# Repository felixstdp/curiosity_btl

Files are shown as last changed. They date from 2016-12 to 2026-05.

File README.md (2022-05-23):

# curiosity_btl
files for Curiosity Bricolabs Technology Laboratory project

scale_1_10 folder for 1:10 scale model (this model has evolved to [Perseverance](https://github.com/felixstdp/Perseverance))
- 4 x 9g servos
- 6 x N20 dc motors

scale_1_5 folder for 1:5 scale model
- 4 x s3003/996 servos
- 6 x type 25D/2418 dc motors
- 2 x RC car steering turnbuckle
- 2S High capacity LiPo battery (e.g. https://www.batteryspace.com/li-ion-battery-14-8v-5-2ah-77wh-8a-rate-for-diving-light---un-38-3-passed.aspx)

.scad files for OpenScad
.stl files for printing
.ino files for Arduino
.jpg files for images

https://bricolabs.cc/wiki/en/proyectos/curiosity_btl (english)
https://bricolabs.cc/wiki/proyectos/curiosity_btl (spanish)

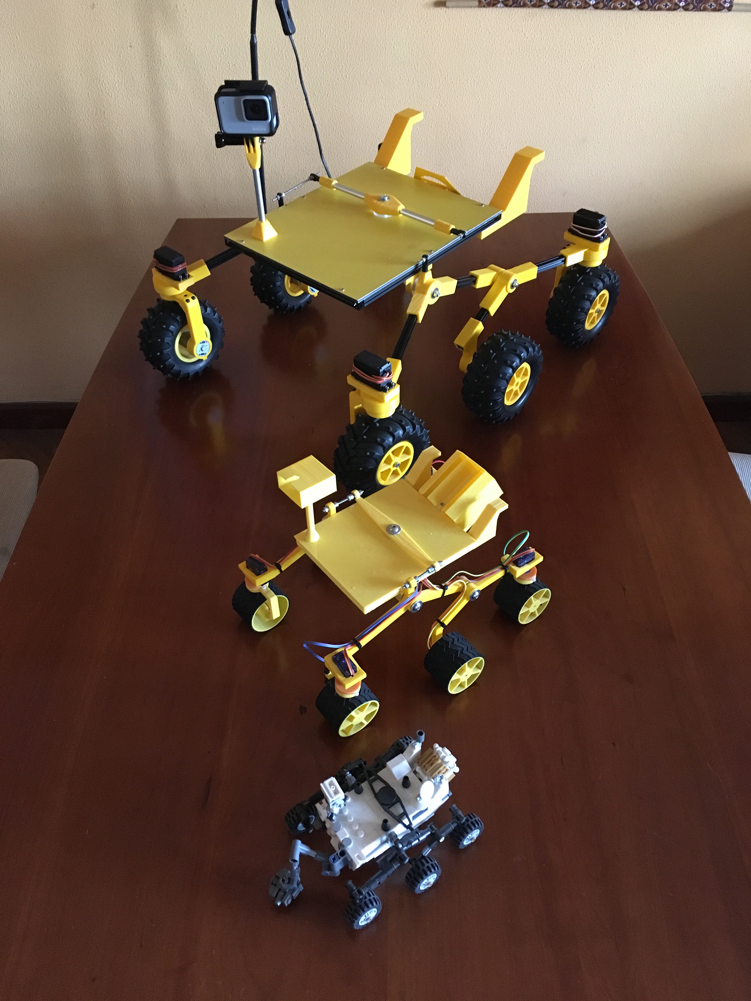
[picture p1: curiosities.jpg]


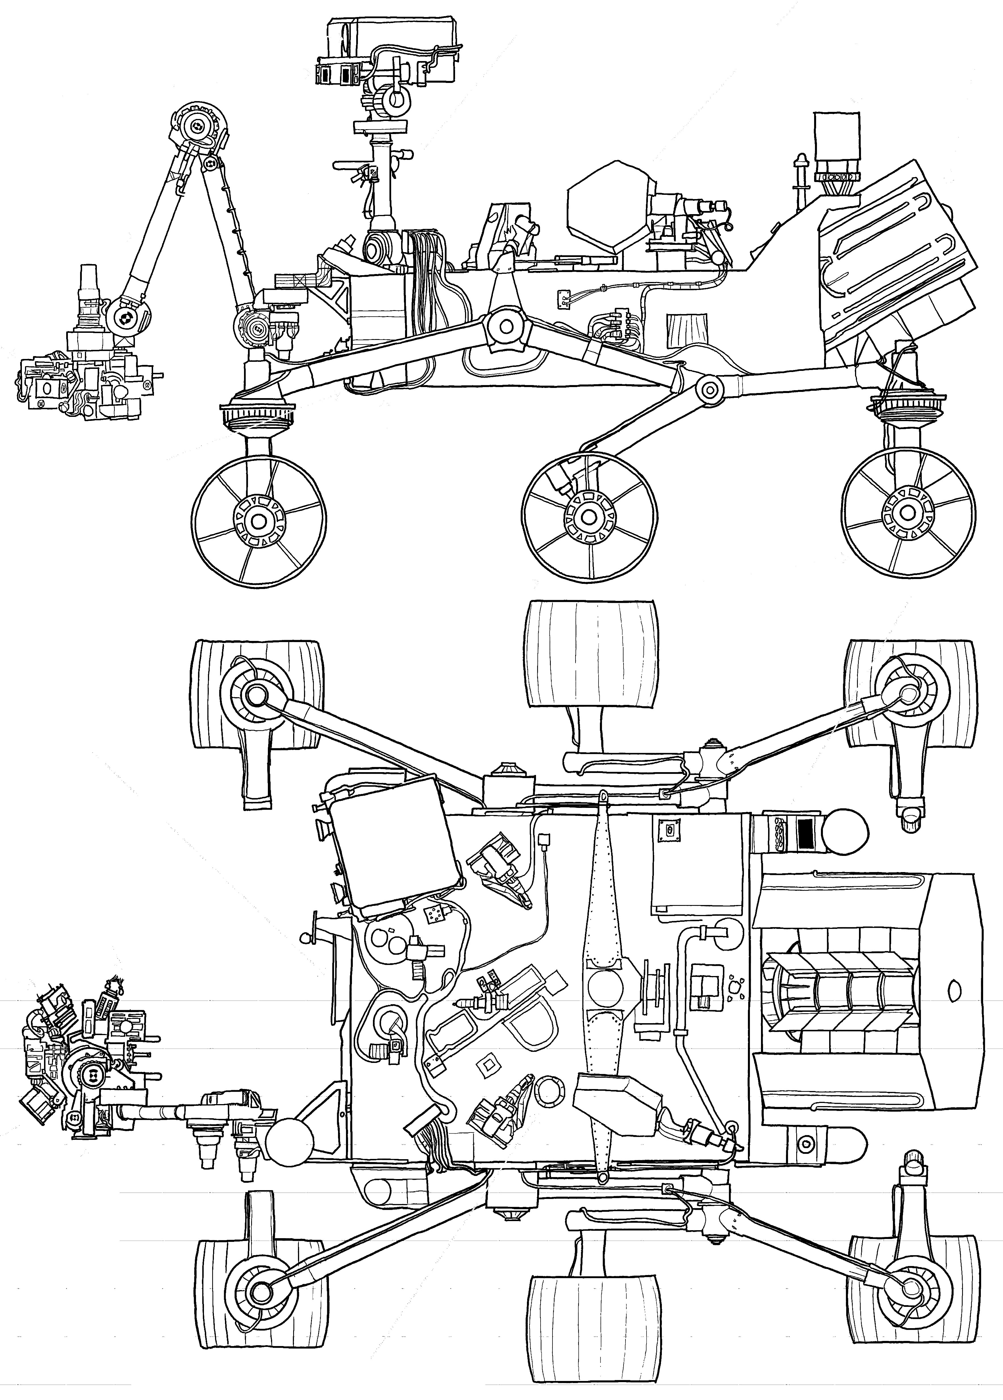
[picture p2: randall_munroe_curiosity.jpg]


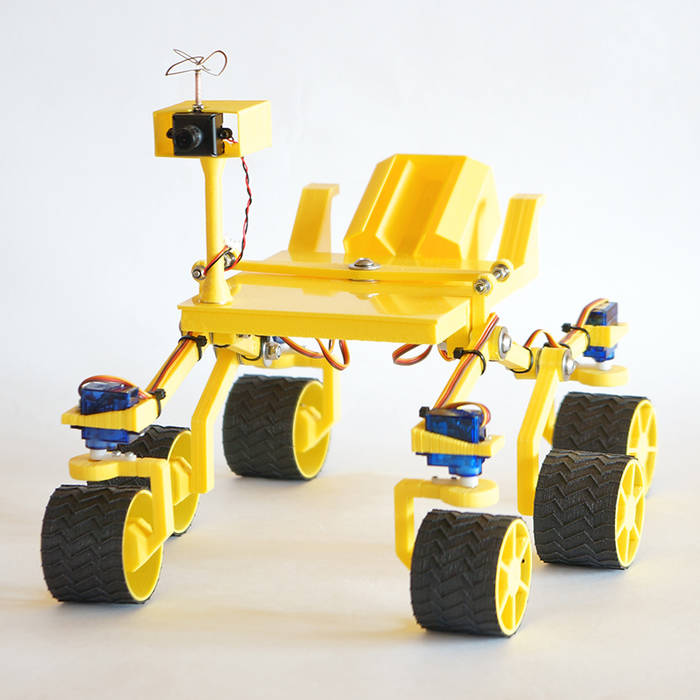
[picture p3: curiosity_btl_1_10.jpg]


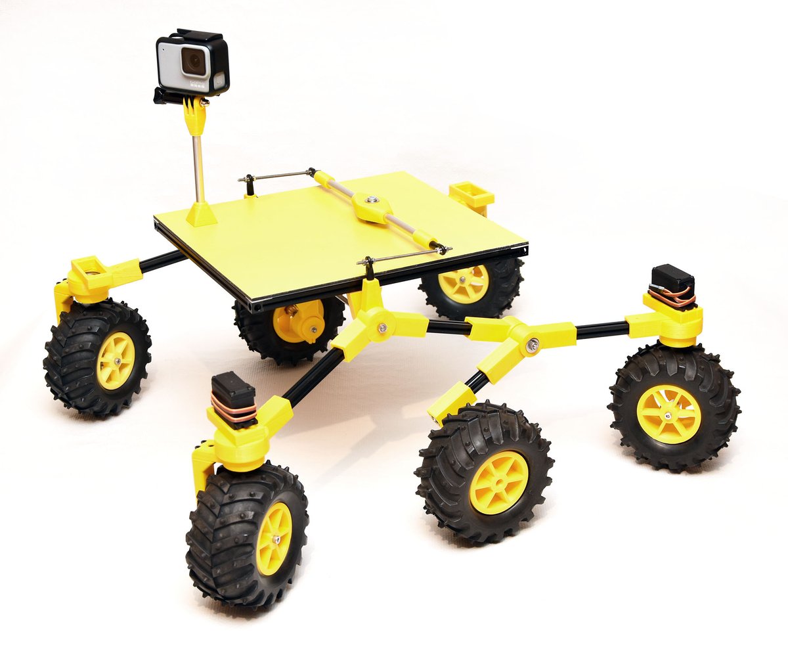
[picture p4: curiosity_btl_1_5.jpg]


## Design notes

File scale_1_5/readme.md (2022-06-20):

Versión con ruedas impresas

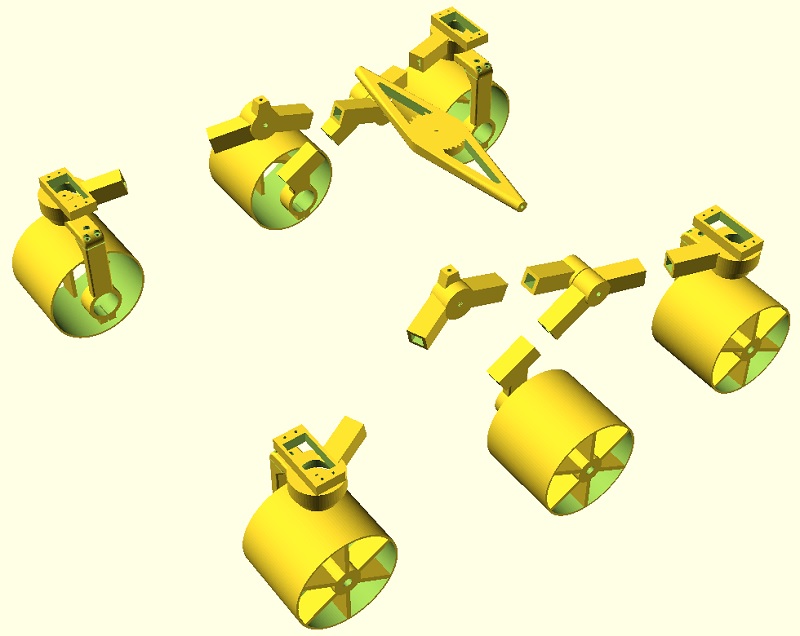
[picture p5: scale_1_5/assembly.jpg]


Versión con ruedas comerciales Pololu Dagu

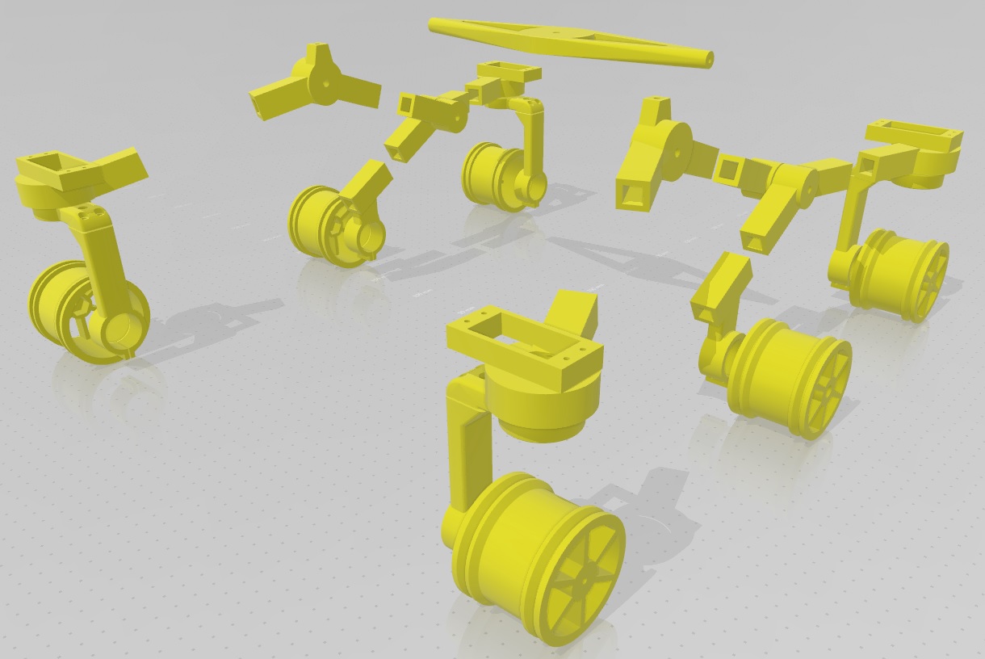
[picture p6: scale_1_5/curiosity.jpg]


BOM

- 4 servos s3003
- 6 motores 2418/25D
- 4 rodamientos 15x35x11
- 8 perfiles de aluminio 10x10mm (2 x 135mm, 2 x 125mm, 2 x 100mm, 2 x 115mm)
- 1 barra roscada M5
- 3 tornillos M5x45 + tuerca autoblocante + arandelas
- 30 tornillos M2.5 + tuerca
- 35 tornillos M3x10
- Plancha de Dibond de 3mm de grosor y 240x280mm. Opcional marco (sencillo/doble) de perfilería por debajo.

Las piezas con nombre 'atrezzo' no son funcionales, sólo decorativas para parecerse más al Curiosity MLS.

La impresión de todas las piezas necesita alrededor de 1kg de plástico y 60-70h. La impresión de las cubiertas (tyre) con material elástico 50-60h.

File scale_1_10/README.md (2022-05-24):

Lecacy code and project only for support.

If new, switch to [Perseverance](https://github.com/felixstdp/Perseverance)

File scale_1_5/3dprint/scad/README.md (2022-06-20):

There are two options for wheels:

- Commercial unit: Pololu Dagu
- 3D printed unit with flexible filament

rims (corner and center) and wheel_bracket_2 for the first options are labeled as 'dagu'.

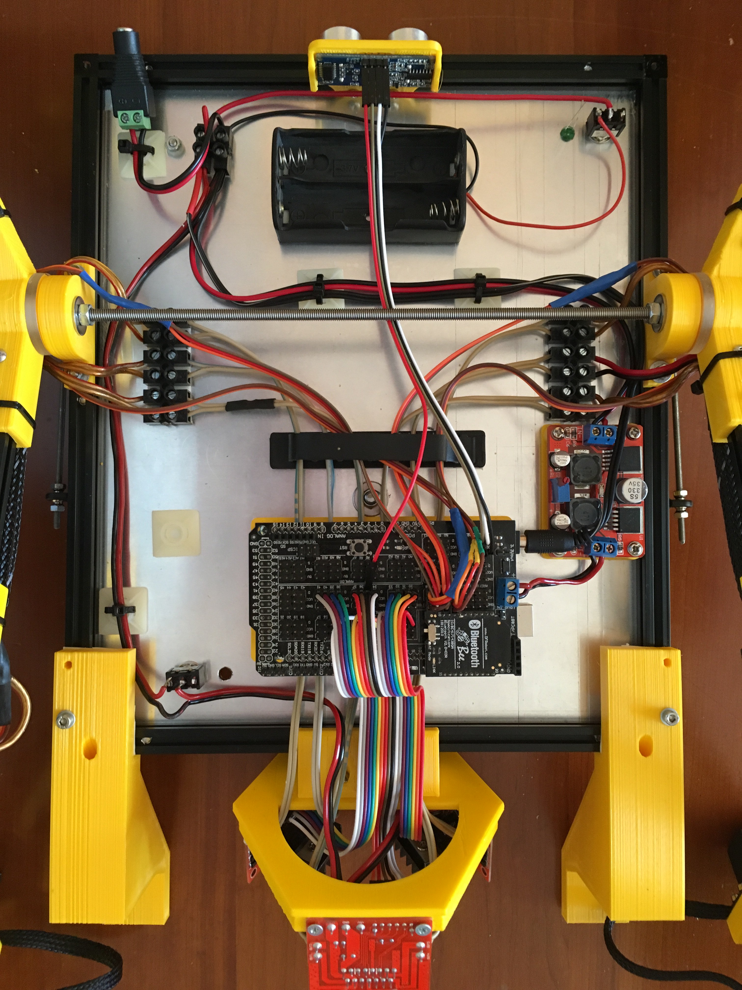
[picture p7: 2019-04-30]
cableado.jpg

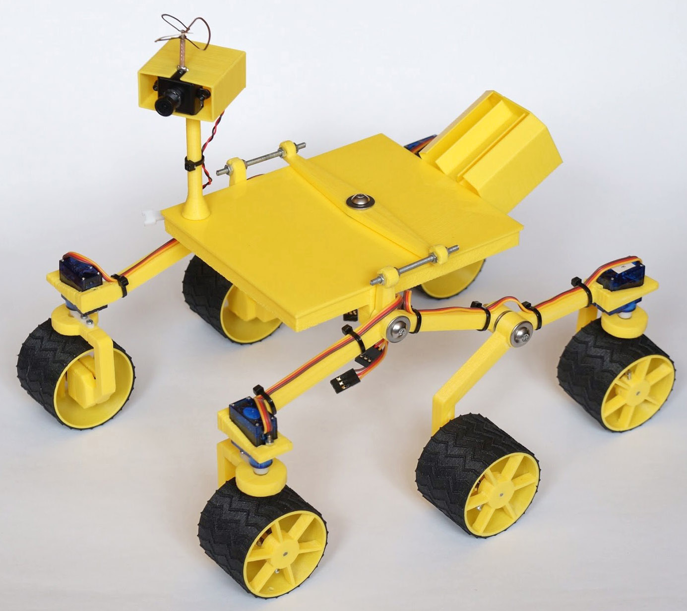
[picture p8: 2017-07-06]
scale_1_10/curiosity_btl.jpg

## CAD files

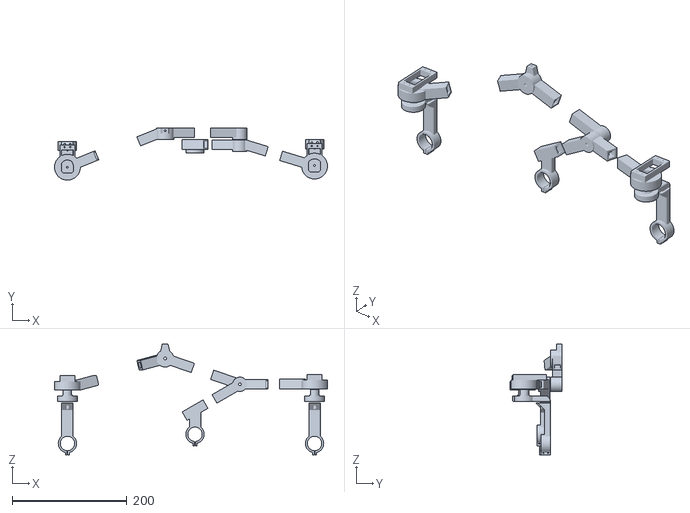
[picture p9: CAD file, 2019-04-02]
scale_1_5/assembly.stl
475.0 x 91.0 x 193.0

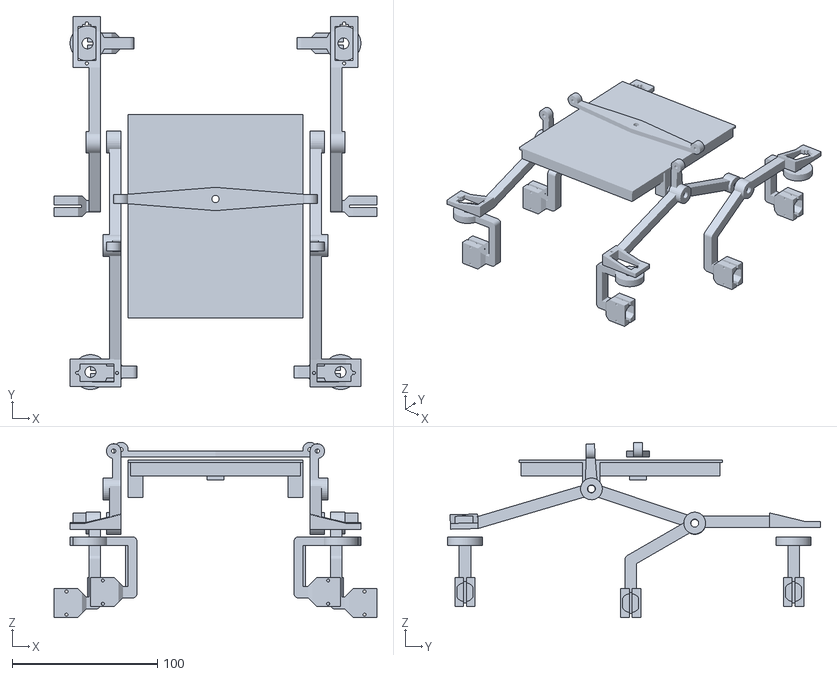
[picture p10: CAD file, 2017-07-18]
scale_1_10/stl/assembly.stl
222.0 x 256.5 x 120.5

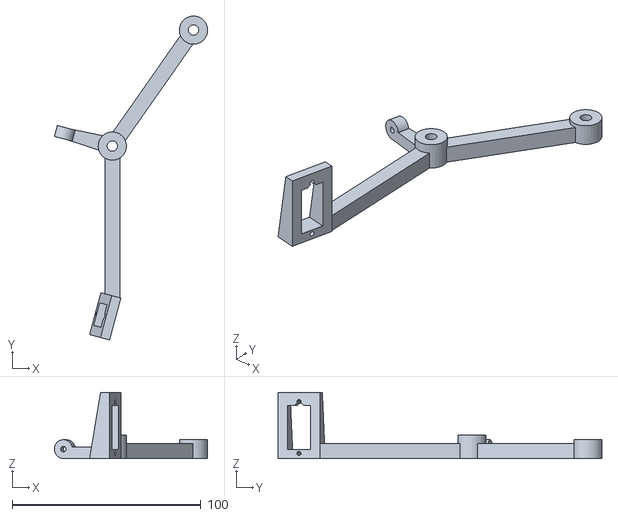
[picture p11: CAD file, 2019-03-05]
scale_1_10/stl/front_bogie.stl
81.2 x 171.7 x 35.0

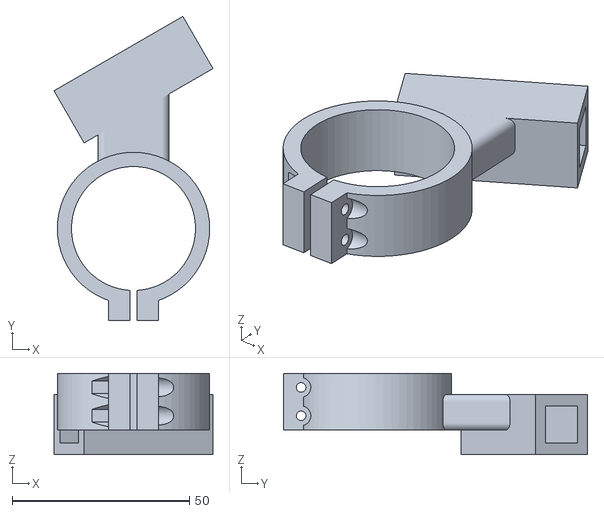
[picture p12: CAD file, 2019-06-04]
scale_1_5/3dprint/35mm_motors/rear_bogie_3_35mm.stl
44.9 x 85.9 x 23.0

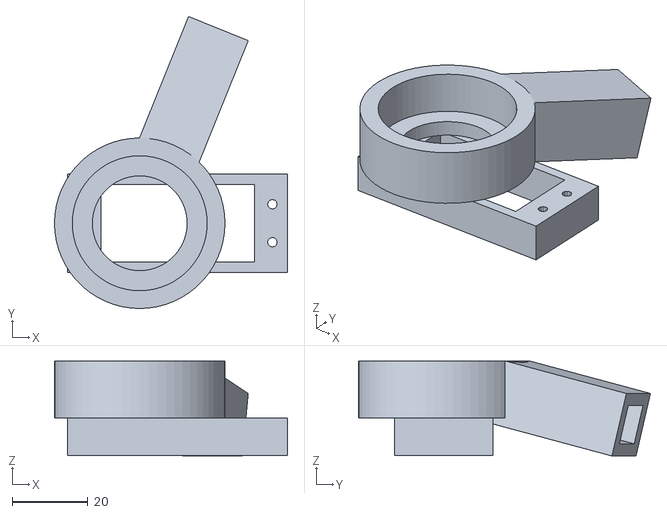
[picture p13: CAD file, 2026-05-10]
scale_1_5/3dprint/stl/front_bogie_1.stl
61.5 x 77.1 x 25.1

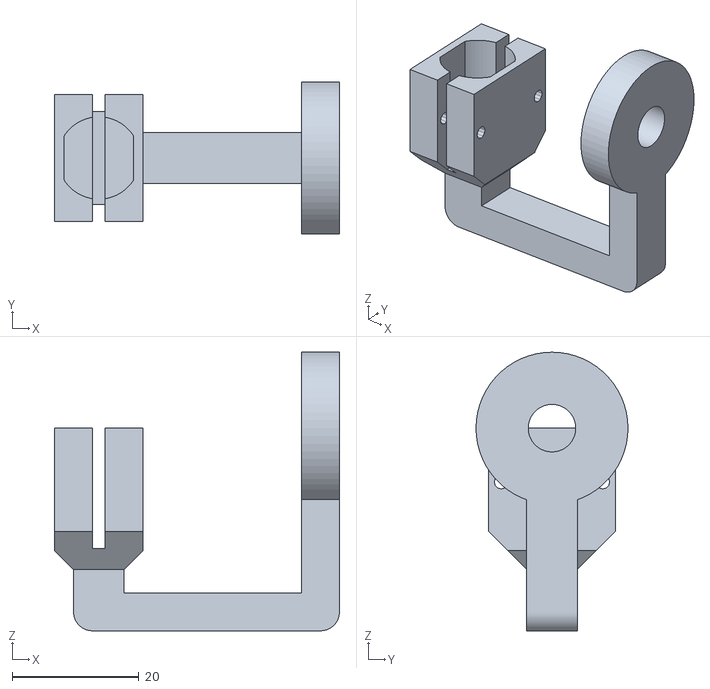
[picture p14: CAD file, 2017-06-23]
wheel_servo_braket.stl
45.0 x 24.0 x 44.0

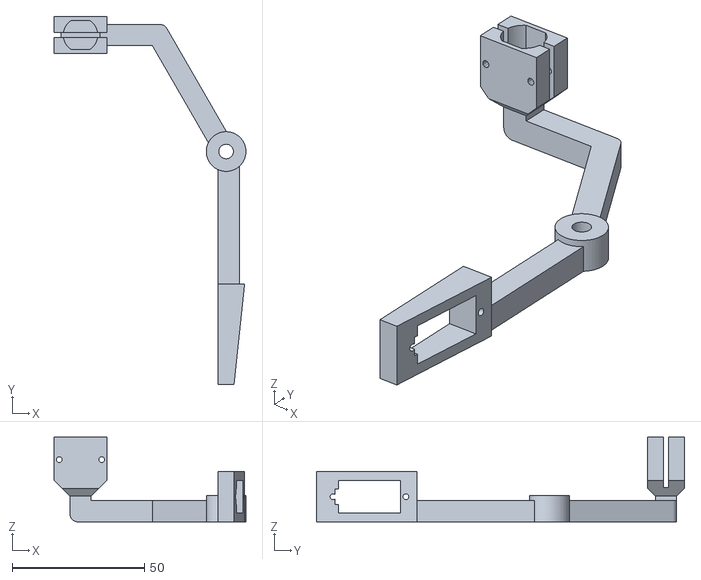
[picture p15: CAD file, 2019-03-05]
scale_1_10/stl/rear_bogie.stl
72.5 x 139.0 x 32.0

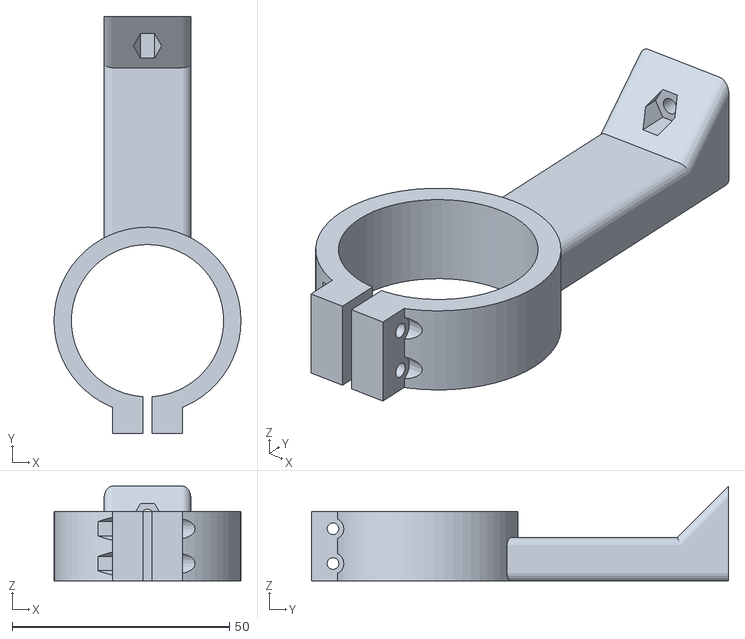
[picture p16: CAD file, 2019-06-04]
scale_1_5/3dprint/35mm_motors/wheel_bracket_1_35mm.stl
43.0 x 96.0 x 21.8

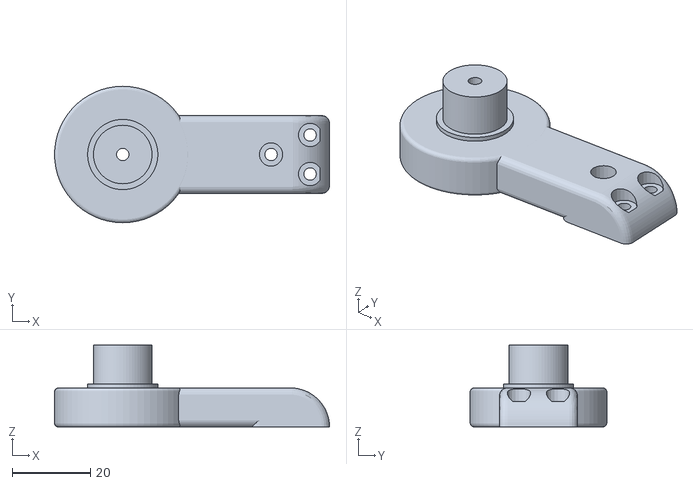
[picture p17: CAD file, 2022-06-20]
scale_1_5/3dprint/stl/wheel_bracket_2.stl
70.5 x 35.0 x 21.0

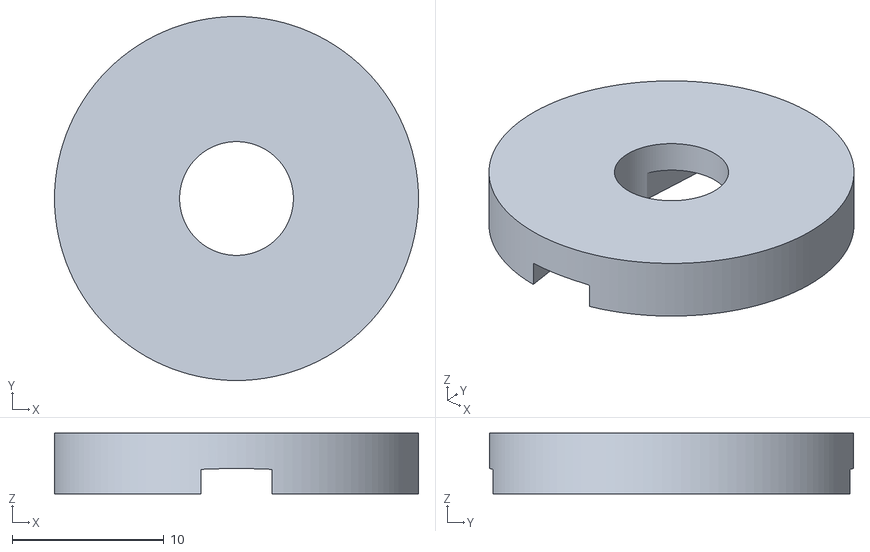
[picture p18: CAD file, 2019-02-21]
scale_1_10/stl/wheel_bracket_sandwich.stl
24.0 x 24.0 x 4.00

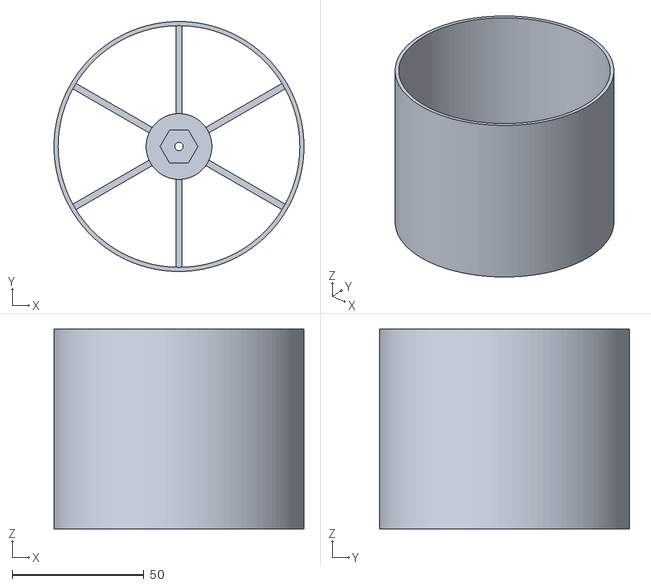
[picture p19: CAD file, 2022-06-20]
scale_1_5/3dprint/stl/corner_rim.stl
95.0 x 95.0 x 76.0

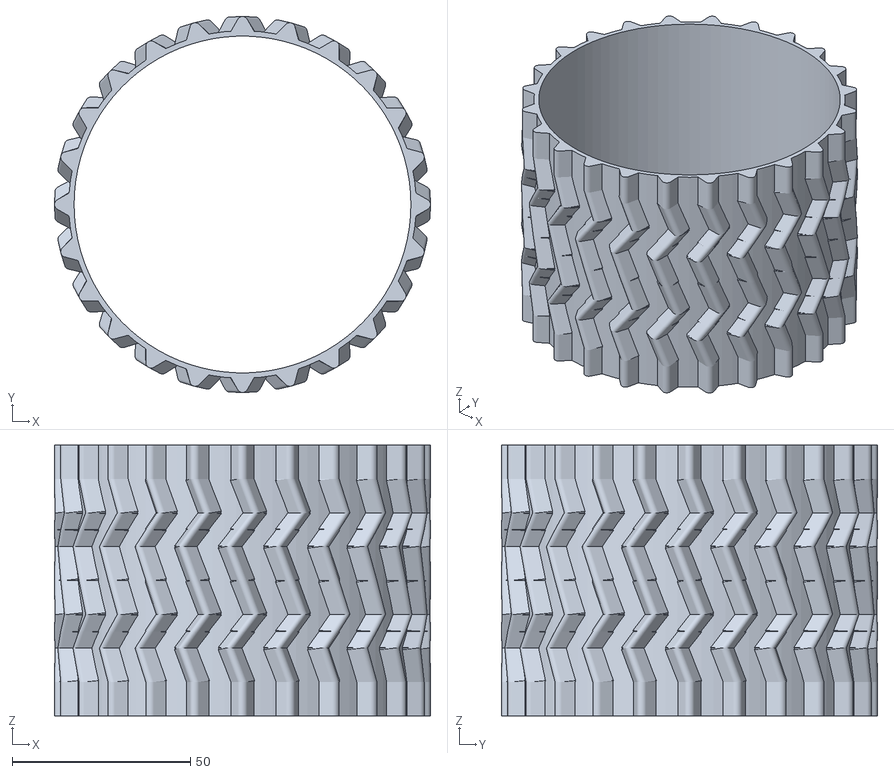
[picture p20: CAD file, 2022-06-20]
scale_1_5/3dprint/stl/tyre.stl
105.5 x 105.5 x 76.0

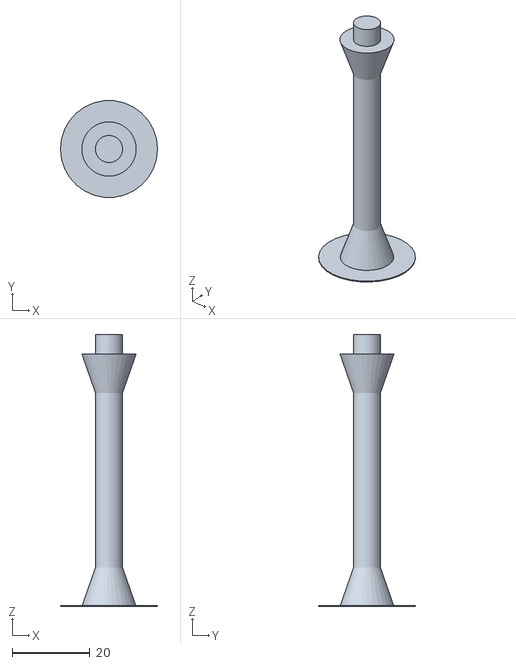
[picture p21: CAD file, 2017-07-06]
scale_1_10/stl/mastcam_post.stl
25.0 x 24.9 x 70.0

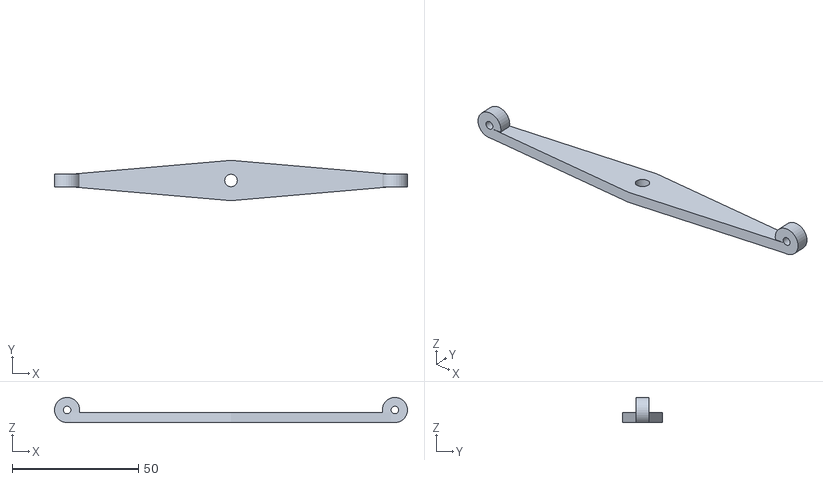
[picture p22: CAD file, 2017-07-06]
scale_1_10/stl/stabilizing_bar.stl
140.0 x 16.0 x 9.97

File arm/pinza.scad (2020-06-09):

$fn=240;
difference(){
union(){
difference(){
    cylinder(d=80,h=10);
    translate([0,0,-1])
    cylinder(d=77,h=12);
}
translate([7.5,0,0])
difference(){
    cylinder(d=65,h=10);
    translate([0,0,-1])
    cylinder(d=62,h=12);
}
translate([0,-.75,0])cube([40,1.5,10]);
rotate([0,0,45])translate([0,-.75,0])cube([40,1.5,10]);
rotate([0,0,67.5])translate([0,-.75,0])cube([40,1.5,10]);
rotate([0,0,90])translate([0,-.75,0])cube([40,1.5,10]);
rotate([0,0,112.5])translate([0,-.75,0])cube([40,1.5,10]);
rotate([0,0,-45])translate([0,-.75,0])cube([40,1.5,10]);
rotate([0,0,-67.5])translate([0,-.75,0])cube([40,1.5,10]);
rotate([0,0,-90])translate([0,-.75,0])cube([40,1.5,10]);
rotate([0,0,-112.5])translate([0,-.75,0])cube([40,1.5,10]);
}
    translate([45,0,-1])cylinder(d=45,h=12);
    translate([7.5,0,0])cylinder(d=62,h=12);
}

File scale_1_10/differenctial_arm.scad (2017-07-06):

$fn=30;

difference(){

linear_extrude(height=4)
polygon(
[[-63.5,2.5],
[0,8],
[63.5,2.5],
[63.5,-2.5],
[0,-8],
[-63.5,-2.5]]);

cylinder(d=5,h=10,center=true);
}

translate([65,0,5])rotate([90,0,0])
difference(){
cylinder(d=10,h=5,center=true);
cylinder(d=3,h=7,center=true);
}

translate([-65,0,5])rotate([90,0,0])
difference(){
cylinder(d=10,h=5,center=true);
cylinder(d=3,h=7,center=true);
}

translate([60,-2.5,0])
cube([5,5,1.5]);

translate([-65,-2.5,0])
cube([5,5,1.5]);

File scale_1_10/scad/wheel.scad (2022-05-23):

$fn=120;
difference(){
cylinder(d=47,h=38);
translate([0,0,-1])cylinder(d=45,h=40);
}
difference(){
union()
{
for(i=[0:60:300])
{
    rotate([0,0,i])translate([3,-0.75,0])
    cube(size=[20,1.5,10]);
} 
cylinder(d=16,h=10);
}
translate([0,0,-1])cylinder(d=3.35,h=21);
}
rotate([0,0,30])translate([1.15,-2,0])
cube(size=[2,4,10]);

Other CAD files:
scale_1_5/3dprint/stl/center_rim.stl
scale_1_5/3dprint/stl/rear_bogie_3.stl
scale_1_10/stl/mastcam_box.stl
scale_1_5/3dprint/stl/wheel_bracket_1.stl
scale_1_10/scad/wheel_bracket.scad
scale_1_10/mastcam_box.scad
scale_1_10/rtg.scad
scale_1_10/rtg_support.scad
scale_1_10/scad/assembly.scad
scale_1_10/scad/body_top.scad
scale_1_10/scad/front_bogie.scad
scale_1_10/scad/mastcam_box.scad
scale_1_10/scad/mastcam_post.scad
scale_1_10/scad/rear_bogie.scad
scale_1_10/scad/rear_support.scad
scale_1_10/scad/rtg.scad
scale_1_10/scad/rtg_support.scad
scale_1_10/scad/stabilizing_bar.scad
scale_1_10/scad/tyre.scad
scale_1_10/scad/wheel_bracket_r.scad
scale_1_10/scad/wheel_bracket_sandwich.scad
scale_1_10/stl/body_top.stl
scale_1_10/stl/rear_support.stl
scale_1_10/stl/rtg.stl
scale_1_10/stl/rtg_support.stl
scale_1_10/stl/tyre.stl
scale_1_10/stl/wheel.stl
scale_1_10/stl/wheel_bracket.stl
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

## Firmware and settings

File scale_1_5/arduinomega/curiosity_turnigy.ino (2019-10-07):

//       FRONT
//  M1S1       M6S6
//    \         /
//     \       /
//  M2-----------M5
//     /       \
//    /         \
//  M3S3       M4S4
//        REAR

#include <Servo.h>

#define s1center 85 // posiciones de centrado de los servos
#define s3center 95
#define s4center 100
#define s6center 80

#define s1giro 135 // posiciones de giro
#define s3giro 45
#define s4giro 150
#define s6giro 35

Servo servo1;
Servo servo3;
Servo servo4;
Servo servo6;

#define chnum 8 // numero de canales de la emisora
int chval[chnum]; // valores de los canales
int PPMpin = 12; // pin de entrada PPM

void setup()
{

  for (int i = 2; i <= 7; i++)
  {
    pinMode(i,OUTPUT); //pines PWM para velocidad
  }
  for (int i = 34; i <= 46; i++)
  {
    pinMode(i,OUTPUT); //pines digitales para control de dirección
  }
   pinMode(PPMpin, INPUT); //pin de la emisora RC
  
  servo1.attach(10); //pines para servos
  servo3.attach(11);
  servo4.attach(8);
  servo6.attach(9);
  
  servo1.write(s1center); //arranque en posicion central
  servo3.write(s3center);
  servo4.write(s4center);
  servo6.write(s6center);
  
  Serial.begin(9600);
}

void loop()
{
  chval[chnum] = readppm(); //lee la emisora RC

  int throttle=(chval[2]-1000)/17*10; // mando adelante-atras -255 +255
  int turn=(chval[0]-1000)/16; // mando giro 
  int vrot=(chval[3]-1000)/17*10; // mando pivote

//  for(int i = 0; i < chnum; i++) // monitor de señal PPM de la emisora
//  {
//    Serial.print((chval[i]-1000)/17*10);
//    Serial.print("\t");
//  }
//  Serial.println();
  
  if (chval[5]<1000)
  {
    drive(throttle,turn);
  }
  else
  {
    rotate(vrot);
  }
  
  delay(100);
    
}

int readppm()
{
  while(pulseIn(PPMpin, HIGH, 10000)<2000){} //espera al canal 0
  
  for(int i=0; i<chnum; i++)
  {
    chval[i]=pulseIn(PPMpin, HIGH, 10000);
  }
  
  // devuleve el resultado
  return chval[chnum];
}  

void setmotor(int m, int v)
{
  int pwm = 8-m;
  int dir1 = 32+2*m;
  int dir2 = 33+2*m;
  v = constrain(v,-255,255);
  digitalWrite(dir1,v<0);
  digitalWrite(dir2,v>=0);
  analogWrite(pwm,abs(v));
}

void drive(int v, int g)
{
  servo1.write(s1center+g); //posicion recta
  servo3.write(s3center-g);
  servo4.write(s4center-g);
  servo6.write(s6center+g);
  setmotor(1,v);
  setmotor(2,v);
  setmotor(3,v);
  setmotor(4,v);
  setmotor(5,v);
  setmotor(6,v);
}

void rotate(int v)
{
  servo1.write(s1giro); //posicion giro
  servo3.write(s3giro);
  servo4.write(s4giro);
  servo6.write(s6giro);
  setmotor(1,v);
  setmotor(2,v);
  setmotor(3,v);
  setmotor(4,-v);
  setmotor(5,-v);
  setmotor(6,-v);
}

void brake()
{
setmotor(1,0);
setmotor(2,0);
setmotor(3,0);
setmotor(4,0);
setmotor(5,0);
setmotor(6,0);
}

void balizargb(boolean r, boolean g, boolean b)
{
  digitalWrite(19,r); //rojo
  digitalWrite(20,g); //verde
  digitalWrite(21,b); //azul
}

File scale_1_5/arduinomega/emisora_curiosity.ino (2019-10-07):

#define chnum 8 // numero de canales de la emisora
int chval[chnum]; // valores de los canales
int PPMpin = 4; // pin de entrada PPM

void setup()
{
 Serial.begin(9600); 
 pinMode(PPMpin, INPUT); 
}

void loop()
{
  chval[chnum] = readppm();
  
  for(int i = 0; i < chnum; i++) 
  {
    Serial.print(chval[i]); // muestra los valores por el puerto serie
    Serial.print("\t");
  }
  Serial.println();
  delay(200);  
}

int readppm()
{
  while(pulseIn(PPMpin, HIGH, 10000)<2000){} //espera al canal 0
  
  for(int i=0; i<chnum; i++)
  {
    chval[i]=pulseIn(PPMpin, HIGH, 10000); //lee secuencialmente todos los canales
  }
  
  return chval[chnum]; // devuleve el resultado
}  

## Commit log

2016-02-23 Tyre for Curiosity BTL project
    To be printed in FilaFlex or similar.
    [tyre.scad]
2016-02-23 Tyre for Curiosity BTL project
    To be printed with FilaFlex or similar
    [tyre.stl]
2016-02-23 Wheel servo bracket for Curiosity BTL project
    Bracket to assembly front and rear wheels to the direction servomotor
    [wheel_servo_bracket.stl]
2016-02-24 Center wheel bracket for Curiosity BTL
    Bracket and half rocker for rear bogie
    [center_wheel_bracket.scad]
2016-02-24 Center wheel bracket for Curiosity BTL
    wheel bracket and half rear bogie
    [center_wheel_bracket.stl]
2016-02-24 Rear bogie pin for Curiosity BTL
    Pin to assemble rear and center wheel bracket in Coriosity BTL rear bogie. Left side (mirror for right side).
    [rear_bogie_pin.scad]
2016-02-25 Rear bogie pin and bracket for Curiosity BTL
    Add the center wheel bracket and you can assemble the rear bogie for left side. Mirror the pieces for right side
    [rear_bogie_pin.stl, rear_servo_bracket.stl]
2016-12-07 Create wheelrim.scad
    Llanta para neumático off-road
    [wheelrim.scad]
2016-12-07 Create wheelbracket
    soporte para rueda con motoro independiente
2016-12-07 Rename wheelbracket to wheelbracket.scad
    soporte para rueda offroad con motor integrado
    [wheelbracket.scad]
2019-03-05 Update front_bogie.scad
    reinforced servo support
    [front_bogie.scad]
2019-03-05 Update rear_bogie.scad
    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
    [rear_bogie.scad]
2019-04-05 Update and rename gopro_support.scad to mastcam_gopro.scad
    [mastcam_gopro.scad]
2019-04-05 Update and rename rtg.scad to rtg_atrezzo.scad
    [rtg_atrezzo.scad]
2019-04-19 Update and rename stabilizer_bar_1.scad to stabilizer_bar.scad
    [stabilizer_bar.scad, stabilizer_bar_1.scad]
2022-06-23 Update and rename rtg_driver_support.scad to rtg_driver_assy.scad
    [rtg_driver_assy.scad]
